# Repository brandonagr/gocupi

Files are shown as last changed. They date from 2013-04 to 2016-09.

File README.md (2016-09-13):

Create Thick TSP
================
forked the code in order to draw thicker lines to get more contrast. For detailed descriptions see file createThickTSP

gocupi
======

Polargraph (vertical plotter / drawing machine) written in Go. Inspired by [Polargraph](http://www.polargraph.co.uk/) and [drawbot](http://marginallyclever.com/blog/drawbot/) projects, designed with the help of the [Dallas Makerspace](http://dallasmakerspace.org/)

Gocupi is different from existing systems in that it uses a Raspberry Pi to do most of the processing instead of relying on a microcontroller to parse commands. This gives it the ability to render complex svg files and patterns that would not fit in memory on a microcontroller.

**A kit with all the hardware needed is now [available at gocupi.com](http://www.gocupi.com/store/)**

Check out the [project page](http://brandonagr.github.io/gocupi/) for a general description, there are also several [wiki pages](https://github.com/brandonagr/gocupi/wiki) with additional information as well as a [forum](http://4um.gocupi.com).

Custom Linux Distro
===================

You can now [download](https://www.dropbox.com/s/6l89m04kcqiwlgb/gocupi_boot_image.zip?dl=0) a custom linux distrobution built from Raspbian with all gocupi software pre-installed.
Unzip the download and copy files to blank SD card (do not build the image). Put the card in the Pi and Bob's your uncle.

If you choose the method above (custom linux distro) then you can skip to the bottom of this document to section "Run gocupi".

Manual Installation Quickstart Guide
================

(Start with something well supported i.e. Raspbian Wheezy.) 

Install Go
-----------
The full install guide is on [golang.org](http://golang.org/doc/install). For the Raspberry Pi you can [download precompiled binaries](http://dave.cheney.net/unofficial-arm-tarballs) to avoid the lengthy process of building go from source.

For example, installing go to the default location with a precompiled binary on a raspberry pi just takes 3 commands:

    wget http://dave.cheney.net/paste/go.1.3.linux-arm~multiarch-armv6-1.tar.gz
    sudo tar -C /usr/local -xzf go.1.3.linux-arm~multiarch-armv6-1.tar.gz
    sudo echo 'export PATH=$PATH:/usr/local/go/bin' >> ~/.profile

(You must set GOROOT also if you install go to someplace besides the default /usr/local/go)

Fix the serial communication (for Raspberry Pi)
----------------------------
Change the default serial communication by editing /boot/cmdline.txt and remove references to `/dev/ttyAMA0`

Disable the getty on that serial port in /etc/inittab by commenting out references to `/dev/ttyAMA0`

In order to reset the serial communication port we need to `sudo reboot`

Setup gopath folder
----------------------------
Setup the folder for your gopath and set some path variables

    mkdir ~/gopath
    sudo echo 'export GOPATH=$HOME/gopath' >> ~/.profile
    sudo echo 'export PATH=$PATH:$HOME/gopath/bin' >> ~/.profile

Install needed dependency
---------------------
Update apt-get, install mercurial, and reboot

    sudo apt-get update
    sudo apt-get install mercurial
    sudo reboot

Download and build gocupi
---------------------------
From your home directory

    go get github.com/brandonagr/gocupi

Run gocupi
----------
`gocupi` The gocupi executable should now be in your $GOPATH\bin folder, you can run the command with no arguments to display the help and what command are available

`gocupi setup 1000 700 700` The setup command can be used to initialize the dimensions of the polargraph hardware, the setup is stored in the generated gocupi_config.xml file

`gocupi -toimage grid 100 10` The -toimage flag causes the system to draw to an output.png instead of trying to control the stepper motors over serial

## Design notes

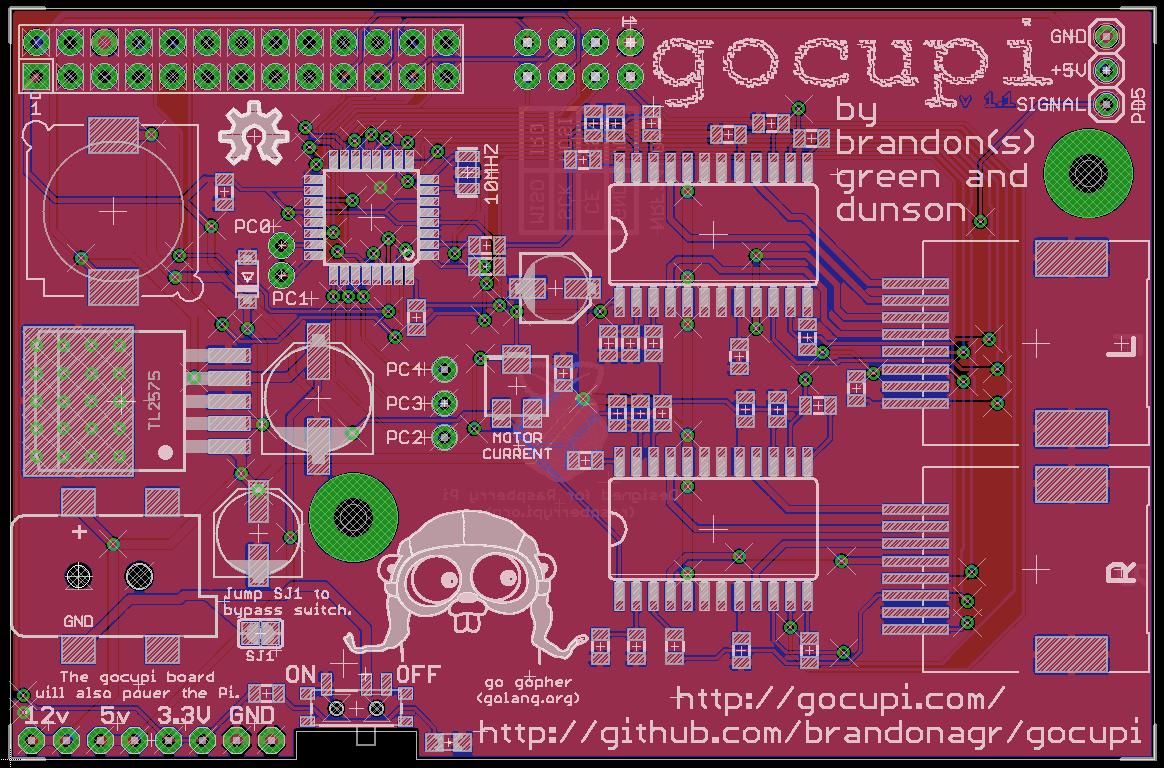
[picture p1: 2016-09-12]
electronics/v1.1/gocupi_v1.1.brd.png

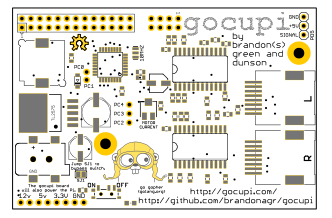
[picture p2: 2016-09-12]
electronics/v1.1/v1.1.png

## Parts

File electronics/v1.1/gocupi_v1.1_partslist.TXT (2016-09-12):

Partlist

Exported from gocupi_v1.1.brd at 9/12/2016 5:10:11 PM

EAGLE Version 6.4.0 Copyright (c) 1988-2013 CadSoft

Assembly variant: 

Part     Value              Package                         Library                     Position (mm)         Orientation

C1       680p               0805                            SparkFun-Passives           (46.51375 8.41375)    R270
C2       100uF              PANASONIC_D                     adafruit                    (18.415 16.8275)      R90
C3       680p               0805                            SparkFun-Passives           (44.45 30.95625)      R270
C4       680p               0805                            SparkFun-Passives           (43.33875 47.3075)    R90
C5       330uF              PANASONIC_F                     adafruit                    (22.86 26.82875)      R90
C7       47uF               PANASONIC_C                     microbuilder                (40.48125 35.08375)   R0
C8       0.1uF              0805                            SparkFun-Passives           (15.875 42.2275)      R270
C9       680p               0805                            SparkFun-Passives           (45.085 25.7175)      R90
CN1                         DCJACK_2MM_SMT                  microbuilder                (5.08 13.6525)        R0
D1                          SOD-123                         dp_devices                  (17.62125 35.71875)   R90
JP1                         1X03-CLEANBIG                   adafruit                    (32.22625 26.51125)   R90
JP2                         1X01-CLEANBIG                   adafruit                    (20.16125 38.25875)   R0
JP3                         1X01-CLEANBIG                   adafruit                    (20.16125 36.03625)   R0
JP4                         1X03                            adafruit                    (81.43875 51.27625)   R90
JP8      Power              1X08-CLEANBIG                   adafruit                    (10.4775 1.42875)     R180
JP9      2X4                2X4                             headers(.1in)               (46.0375 53.34)       R180
L1       220uH              SDR1305                         inductors                   (7.62 40.79875)       R0
LED1                        CHIPLED_0805                    adafruit                    (32.54375 1.27)       R270
R1       10k                0805                            SparkFun-Resistors          (35.40125 36.67125)   R180
R2       1k                 0805                            SparkFun-Resistors          (19.05 4.92125)       R180
R3       20k                0805                            SparkFun-Resistors          (43.815 8.41375)      R90
R4       20k                0805                            SparkFun-Resistors          (46.83125 25.7175)    R270
R5       20k                0805                            SparkFun-Resistors          (46.0375 30.95625)    R90
R6       20k                0805                            SparkFun-Resistors          (44.92625 47.3075)    R270
R7       10k                0805                            SparkFun-Resistors          (35.40125 38.25875)   R180
R8       10k                0805                            SparkFun-Resistors          (30.1625 32.86125)    R90
R9       10k                0805                            SparkFun-Resistors          (62.865 27.6225)      R270
R11      10k                0805                            SparkFun-Resistors          (59.21375 31.4325)    R90
R12      10k                SM-42/43A                       pot                         (37.62375 27.78125)   R270
R13      10k                0805                            SparkFun-Resistors          (47.78375 30.95625)   R90
R14      10k                0805                            SparkFun-Resistors          (49.37125 8.41375)    R90
R15      10k                0805                            SparkFun-Resistors          (60.0075 26.3525)     R0
R16      10k                0805                            SparkFun-Resistors          (59.3725 8.09625)     R90
R17      10k                0805                            SparkFun-Resistors          (56.99125 26.035)     R270
R18      10k                0805                            SparkFun-Resistors          (56.515 47.3075)      R0
R19      10k                0805                            SparkFun-Resistors          (47.625 47.3075)      R270
R20      5k1                0805                            SparkFun-Resistors          (41.11625 28.73375)   R270
R21      0.75               0805                            SparkFun-Resistors          (54.61 26.035)        R270
R22      0.75               0805                            SparkFun-Resistors          (54.2925 8.09625)     R90
R23      0.75               0805                            SparkFun-Resistors          (54.13375 30.00375)   R90
R24      0.75               0805                            SparkFun-Resistors          (53.34 46.51375)      R0
R25      10k                0805                            SparkFun-Passives           (59.53125 46.19625)   R0
R26      10k                0805                            SparkFun-Resistors          (42.545 44.60875)     R0
R27      10k                0805                            SparkFun-Resistors          (48.41875 25.7175)    R270
R28      10k                0805                            SparkFun-Resistors          (42.70375 22.225)     R0
RJ45-L   RJ45_SMD           RJ45_SMD                        rj45_smd                    (76.2 30.95625)       R90
RJ45-R   RJ45_SMD           RJ45_SMD                        rj45_smd                    (76.2 14.12875)       R90
S1                          SWITCH-SPST-SMD-A               SwK-SparkFun                (25.7175 3.81)        R180
SJ1      SJ1                SJ                              jumper                      (18.57375 9.36625)    R180
U1                          TQFP32-08                       SparkFun-DigitalIC          (26.82875 40.3225)    R180
U2       A3967SLB-L         SO24W                           allegro                     (52.22875 39.0525)    R0
U3       A3967SLB-R         SO24W                           allegro                     (52.22875 17.145)     R0
U4       TL2575             TO263_5                         TL2575_new                  (8.255 26.67)         R90
X1       RASPI_BOARD_AB_E2P RASPI_BOARD_AB_EDGES_2DRILL_PAD raspberrypi_bastelstube_v13 (0 0)                 R0
XTAL1    10MHz              RESONATOR-SMD                   SwK-SparkFun                (33.9725 43.65625)    R90

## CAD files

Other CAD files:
cad/motor mount.dwg
cad/small bearing holder.dwg
cad/guide.dwg

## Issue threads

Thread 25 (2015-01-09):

minor request:  When canceling, print the pen location relative to the starting position

andrewshilliday, 2015-01-09:
It would be nice if, when canceling a print, the program would print out the current location of the pen (in mm for each motor to spool) to get the pen back to the original location so that you don't have to recalibrate to start over.

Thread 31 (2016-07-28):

Trying to DIY this. Any thoughts?

campbx, 2016-07-28:
Hey Brandon, sorry couldn't find your DM/Email, so communicating through an issue.

I am trying to DIY this Zen sand garden using your project:
https://vimeo.com/124882379
You can see more videos inside the artist's gallery.

What would it entail to covert Gocupi kit in a horizontal setup?  I will use a Gocupi-controlled Neodymium magnet underneath a glass surface, and sand + metal ball on the top of the surface.

brandonagr, 2016-08-08:
It would take a lot of work to rewrite a large portion of the code to use a more traditional XY based coordinate system instead of the 'polar' system of two string lengths used here. src/plotter/driver.go is the code that converts the XY coordinates to 'polar', everything downstream of that would have to change

scottvr, 2016-08-08:
What brandonagr is certainly correct, however I did successfully use the gocupi horizontally as is. Your surface would need to be sufficiently elevated to pull it off the same way I did my silly hack, but I'll describe it here for posterity.

[post-edit. Whoa! That got long. Apologies. **TL;DR.: If your surface is elevated, you can attach a counterweight to the gondola and have a horizontally-mounted vertical plotter.** :-) You could then attach a strong magnet to the gondola and a glass table sitting over it - in fact, you might just stick some minature casters or bearings on the bottom of something more suited for the purpose than a pen-holder gondola and you can forego the added consideration of keeping the gondola elevated from the surface below it, since you won't then have weight bearing down on a small pen-tip and woblling and such. But I've rambled long enough so I really will stop now.]

The hanging vertical plotter mechanism relies on the magical invisible pulling force of gravity (and thus the weight of the gondola) to keep the string lengths taught and straight. The top of the drawing surface (imagine a line between the two motors) and the two string lengths form a triangle, with the motors and gondola at each vertex.

Briefly, I had the thought that two more motors opposite the original two would be needed for horizontal success, which while not being complex mathematically or programatically to add them, how to set the initial position, keeping all four lines taught and not having the motors battling against each other was to much to entertain for a silly proof of concept.

But then I thought of that invisible "motor" (gravity) pulling downward on the gondola now, and realized only one additional motor would be needed, perhaps on a rod parallell to the invisible line between the "top" motors.. Visions of a truly ludicrous setup with a bottom "slack" stepper perpendicular to the invisible line, with its own X-axis motion briefly made me chuckle before I realized that a rubber band on a spool over a dowel would meet both purposes, although the further the gondola moved away from this rod, the greater the force pulling the gondola toward it and then things I can barely remember about elastic potential energy and unpleasant memories of the physics class I failed where I should have learned it shut down the thought experiment for the moment. But then, with the vision of the horizontal surface, motors on one side, and a rod running the length of the other still rattling around in the back of my head, it occurred to me that I could attach a string with the surprising properties of (nearly) always (nearly) exerting the same amount of horizontal force away fro the steppers which (not) coincidentally happens to be (nearly) exactly 9.8ms^s. Those of you who passed the physics I failed no doubt immediately recognize that as the acceleration of gravity and probably see where I'm going with this.

So... I laid a whiteboard horizontally on the trunk of my '61 Biscayne, which conveniently already had gocupi motor mounts suction-cupped in place (the board, not my car.. but there's a different story for a different time) and a gondola hanging in the center. I affixed a length of string the length of the "height" (these terms are getting confusing as we move our Euclidian plan in 3D space,  for me at least) of the whitboard + the elevation of the now-horizontal whiteboard from the ground. With the edge of the "bottom" (the 2D bottom, from back when it was in a vertical plane... this is why instructional diagrams label things with convenient unambiguous letters, isn't it?) anyway.. with the side of the whiteboard that used to be the bottom now hanging just beyond the edge of the trunk of the Chevy, and using washers, cable and wire guides and fasteners and other various sundries found in my garage, dangled this weighted line from the gondola over the edge of the whiteboard so that the washers now moved vertically up and down with the movement of the gondola on the whiteboard's Y-axis. With just enough weight from the washers to counteract the gravity that is now tending to draw the gondola to the board, and just enough height from the rod/wire guides/whathaveyou, I was able to replicate the vertical conditions faithfully enough to fool the gocupi into drawing for me as if it was still vertical.

If my writing was too confusing - perhaps a visual illustration would help. But I'm not going to take up any more space with ASCII art so I will leave you with this.. Do you remember the old Batman TV series from the 1960's? Do you remember the scenes where Batman and Robin would be scaling the side of a skyscraper by holding a rope hanging from the top of the building? And how even as a kid watching this, the occasional slack in the rope or other visual cues enabled even a 5-year-old to give the TV a side-eyed glare.. and then, with their innocent little imagination-filled heads turned sideways, they have a Eureka! moment when they realize "hey.... they're just walking and the camera is turned sideways!", and that innocence that enables the perfect suspension of disbelief is forever lost? Yeah, will I'm not saying it's like that, but it's like that.

Closed 2016-08-08.

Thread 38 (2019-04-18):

Left and right stop switches.

monte-monte, 2019-04-18:
Hello. I'm building myself a plotter using your code and schematics. On schematics steppers have stop switches which are connected to atmega pins. But strangely I haven't found any code related to them in "StepperDriver.ino". I would like to know which part is outdated here, or those switches are just for future features like auto-calibration that haven't been implemented yet?

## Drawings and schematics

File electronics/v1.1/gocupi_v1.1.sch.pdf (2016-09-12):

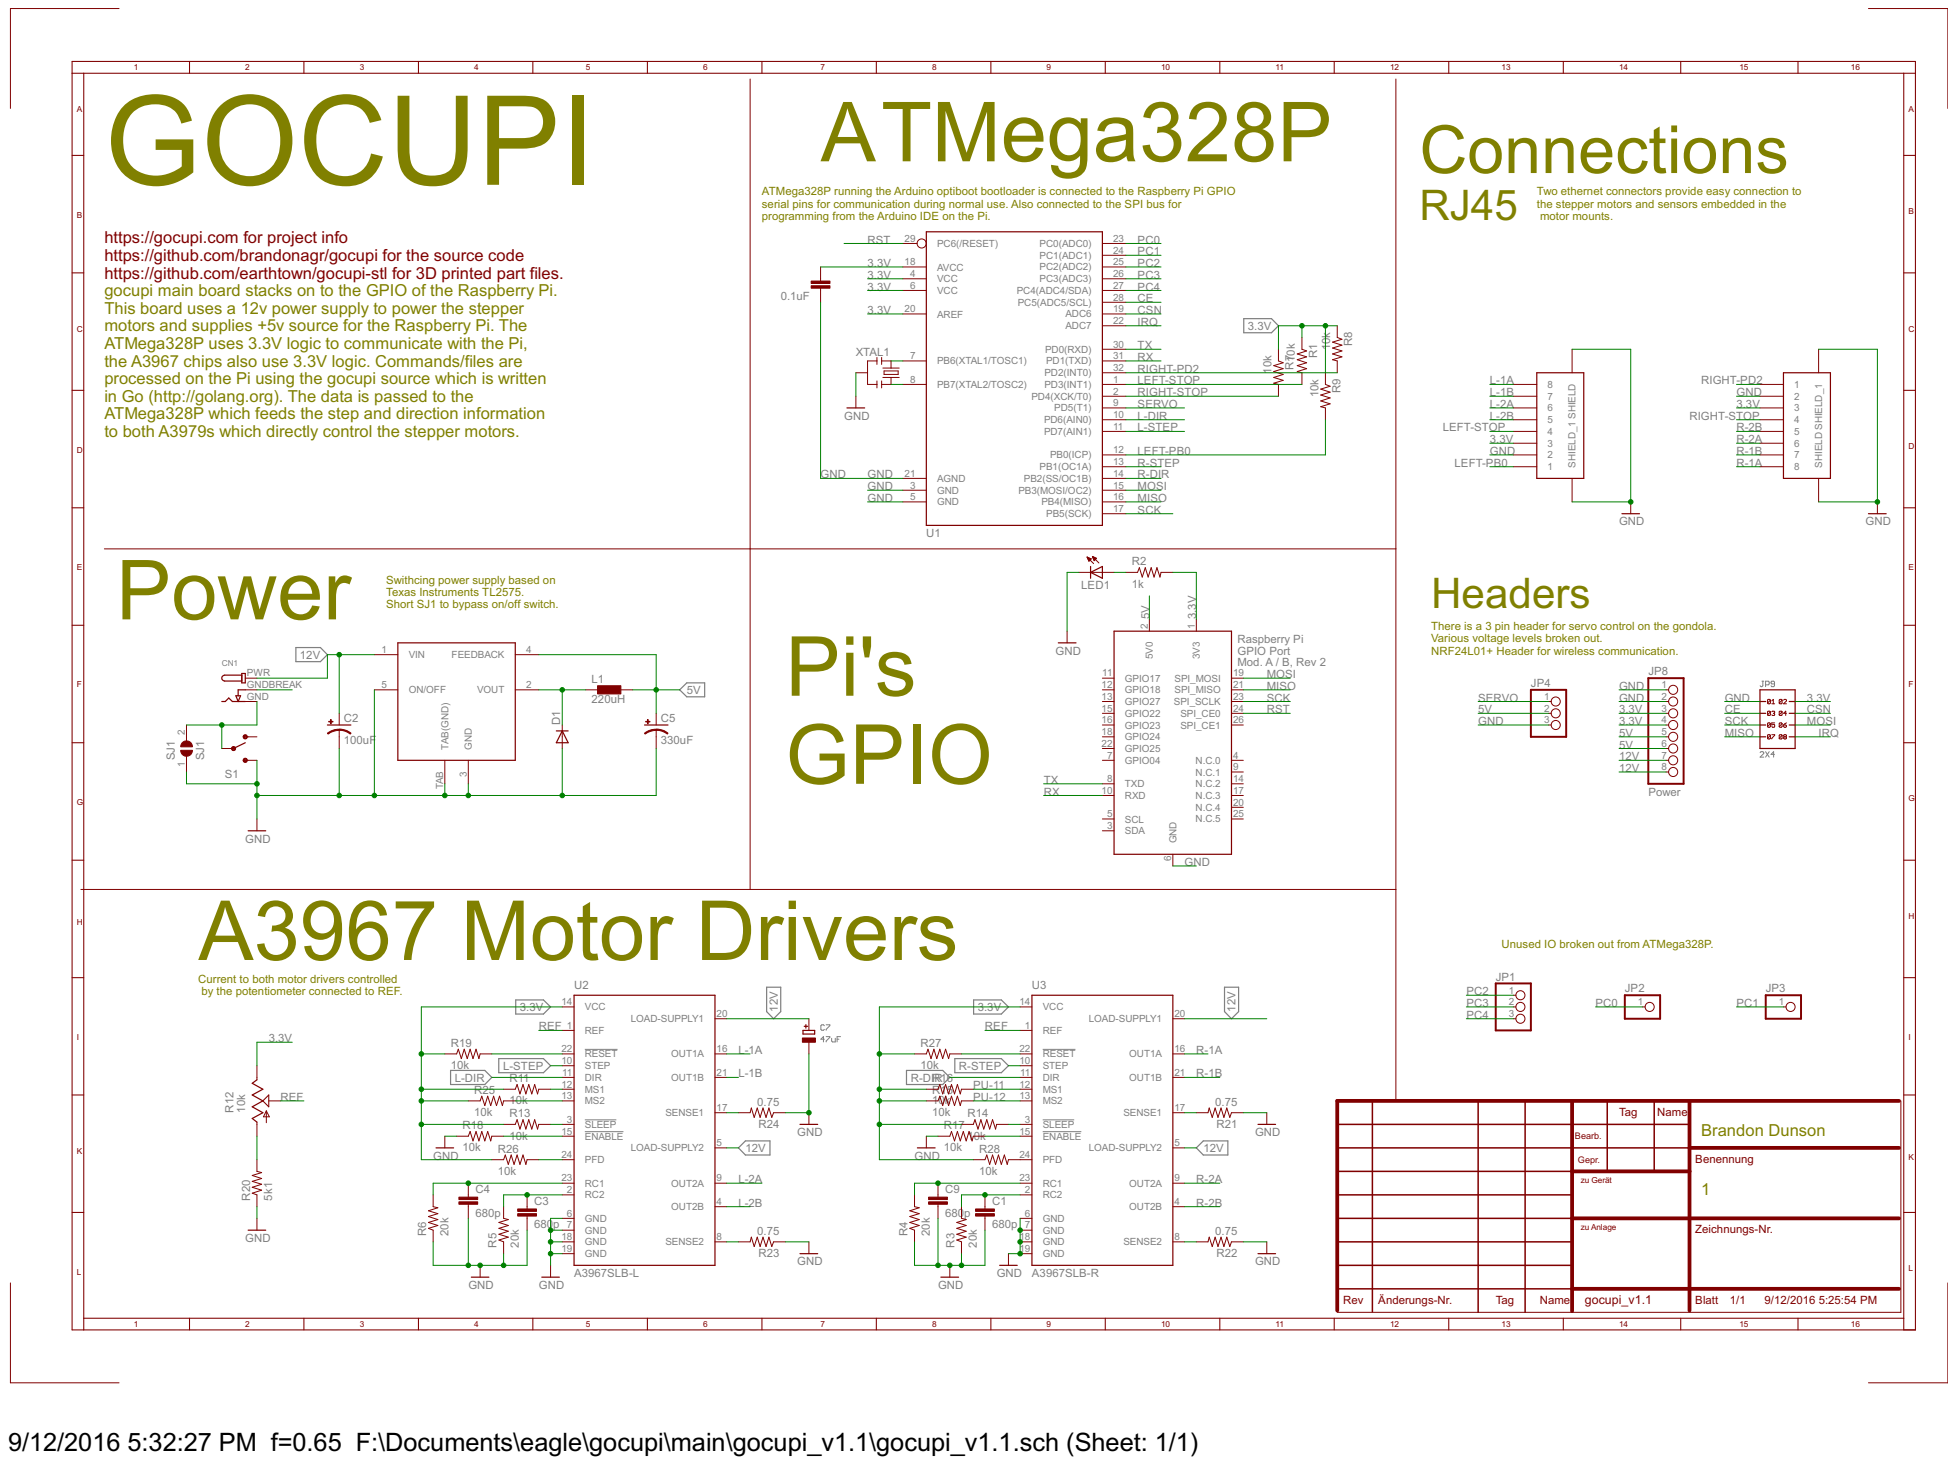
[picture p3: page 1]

ATMega328P ATMega328P running the Arduino optiboot bootloader is connected to the Raspberry Pi GPIO | Connections Two ethernet connectors provide easy connection to the stepper motors and sensors embedded in the motor mounts. | A

https://gocupi.com for project info
https://github.com/brandonagr/gocupi for the source code
https://github.com/earthtown/gocupi-stl for 3D printed part files.
gocupi main board stacks on to the GPIO of the Raspberry Pi. This board uses a 12v power supply to power the stepper motors and supplies +5v source for the Raspberry Pi. The ATMega328P uses 3.3V logic to communicate with the Pi,

the A3967 chips also use 3.3V logic. Commands/files are
processed on the Pi using the gocupi source which is written
in Go (http://golang.org). The data is passed to the ATMega328P which feeds the step and direction information

to both A3979s which directly control the stepper motors.
Power

Short SJ1 to bypass on/off switch. Swithcing power supply based on Texas Instruments TL2575.

Raspberry Pi GPIO Port Mod. A / B, Rev 2 GND

There is a 3 pin header for servo control on the gondola. Various voltage levels broken out. NRF24L01+ Header for wireless communication.

Unused IO broken out from ATMega328P.

Current to both motor drivers controlled
by the potentiometer connected to REF.

9/12/2016 5:32:27 PM f=0.65 F:\Documents\eagle\gocupi\main\gocupi_v1.1\gocupi_v1.1.sch (Sheet: 1/1)

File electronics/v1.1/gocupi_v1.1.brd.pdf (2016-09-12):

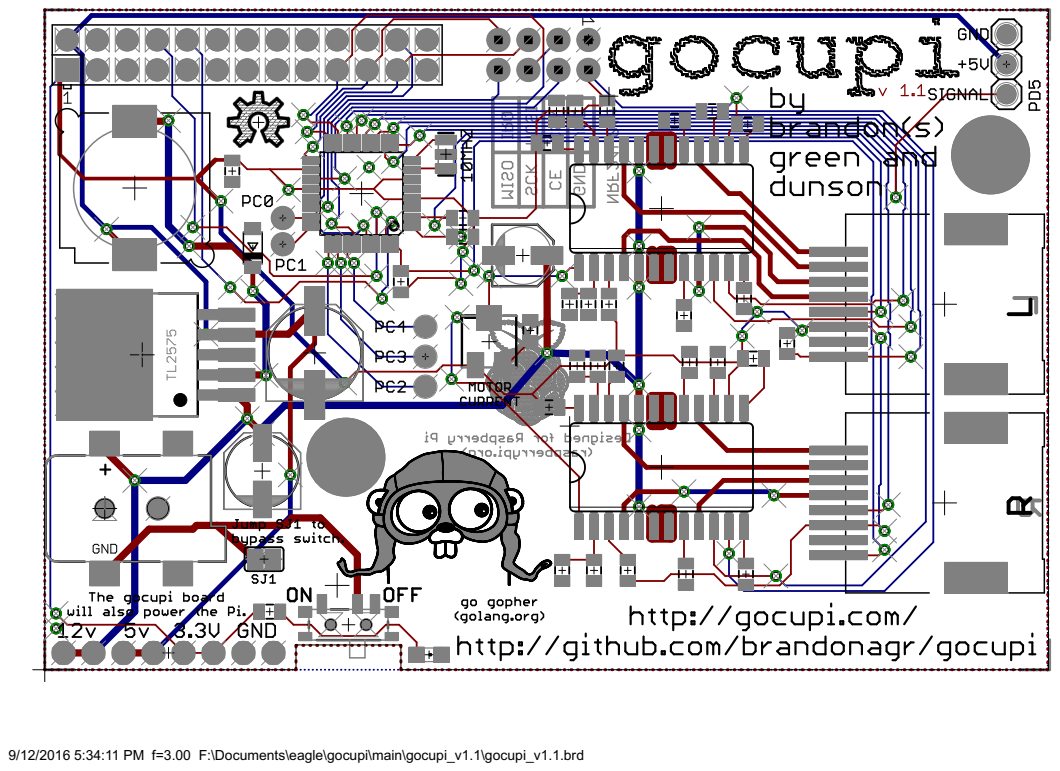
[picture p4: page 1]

9/12/2016 5:34:11 PM f=3.00 F:\Documents\eagle\gocupi\main\gocupi_v1.1\gocupi_v1.1.brd

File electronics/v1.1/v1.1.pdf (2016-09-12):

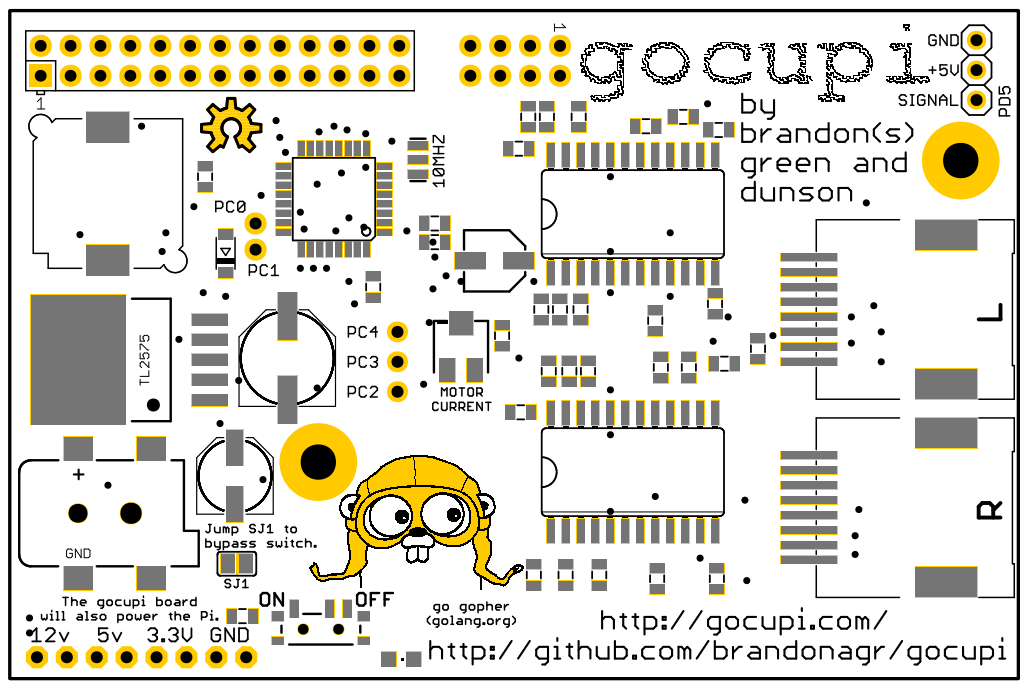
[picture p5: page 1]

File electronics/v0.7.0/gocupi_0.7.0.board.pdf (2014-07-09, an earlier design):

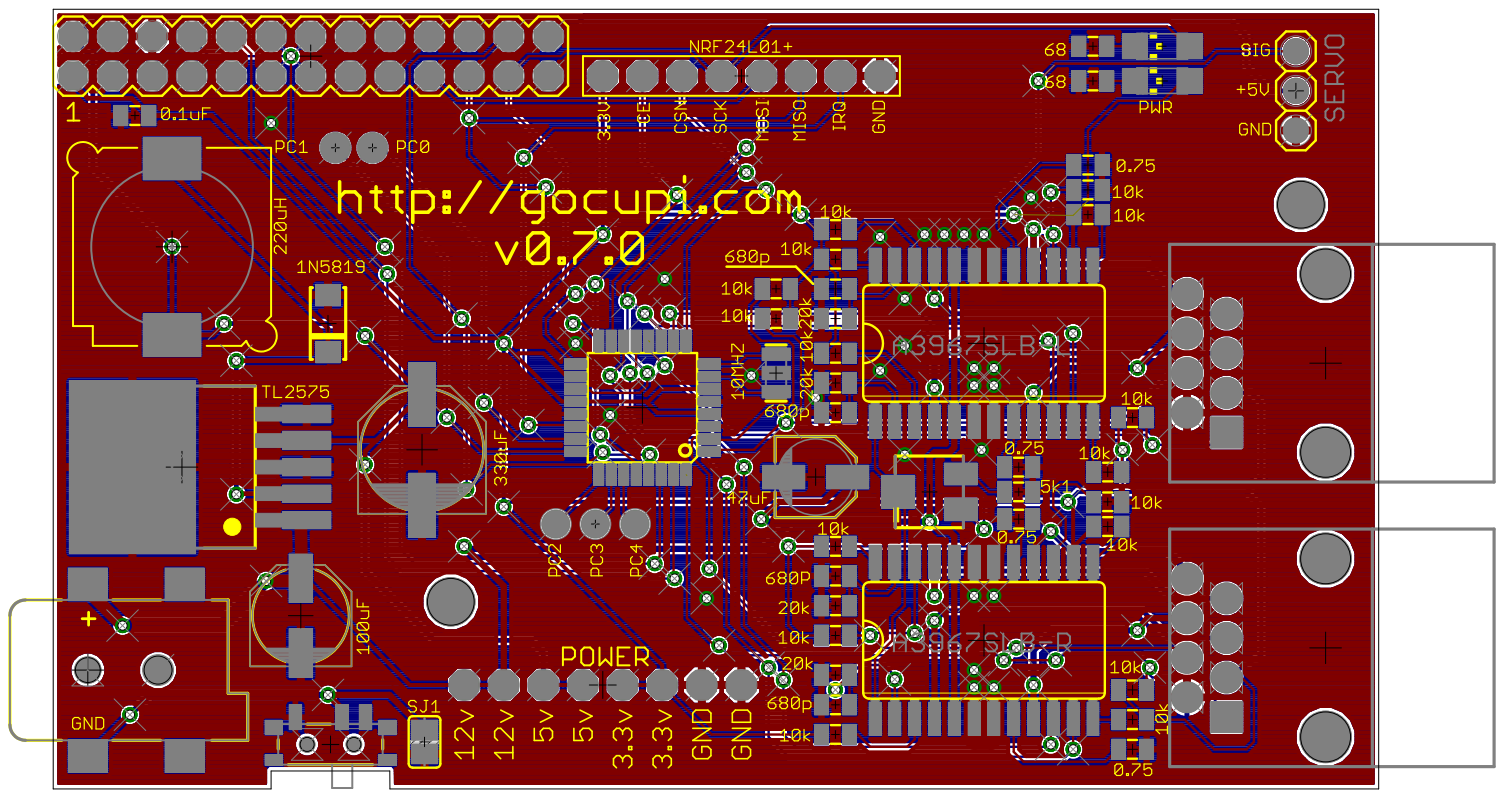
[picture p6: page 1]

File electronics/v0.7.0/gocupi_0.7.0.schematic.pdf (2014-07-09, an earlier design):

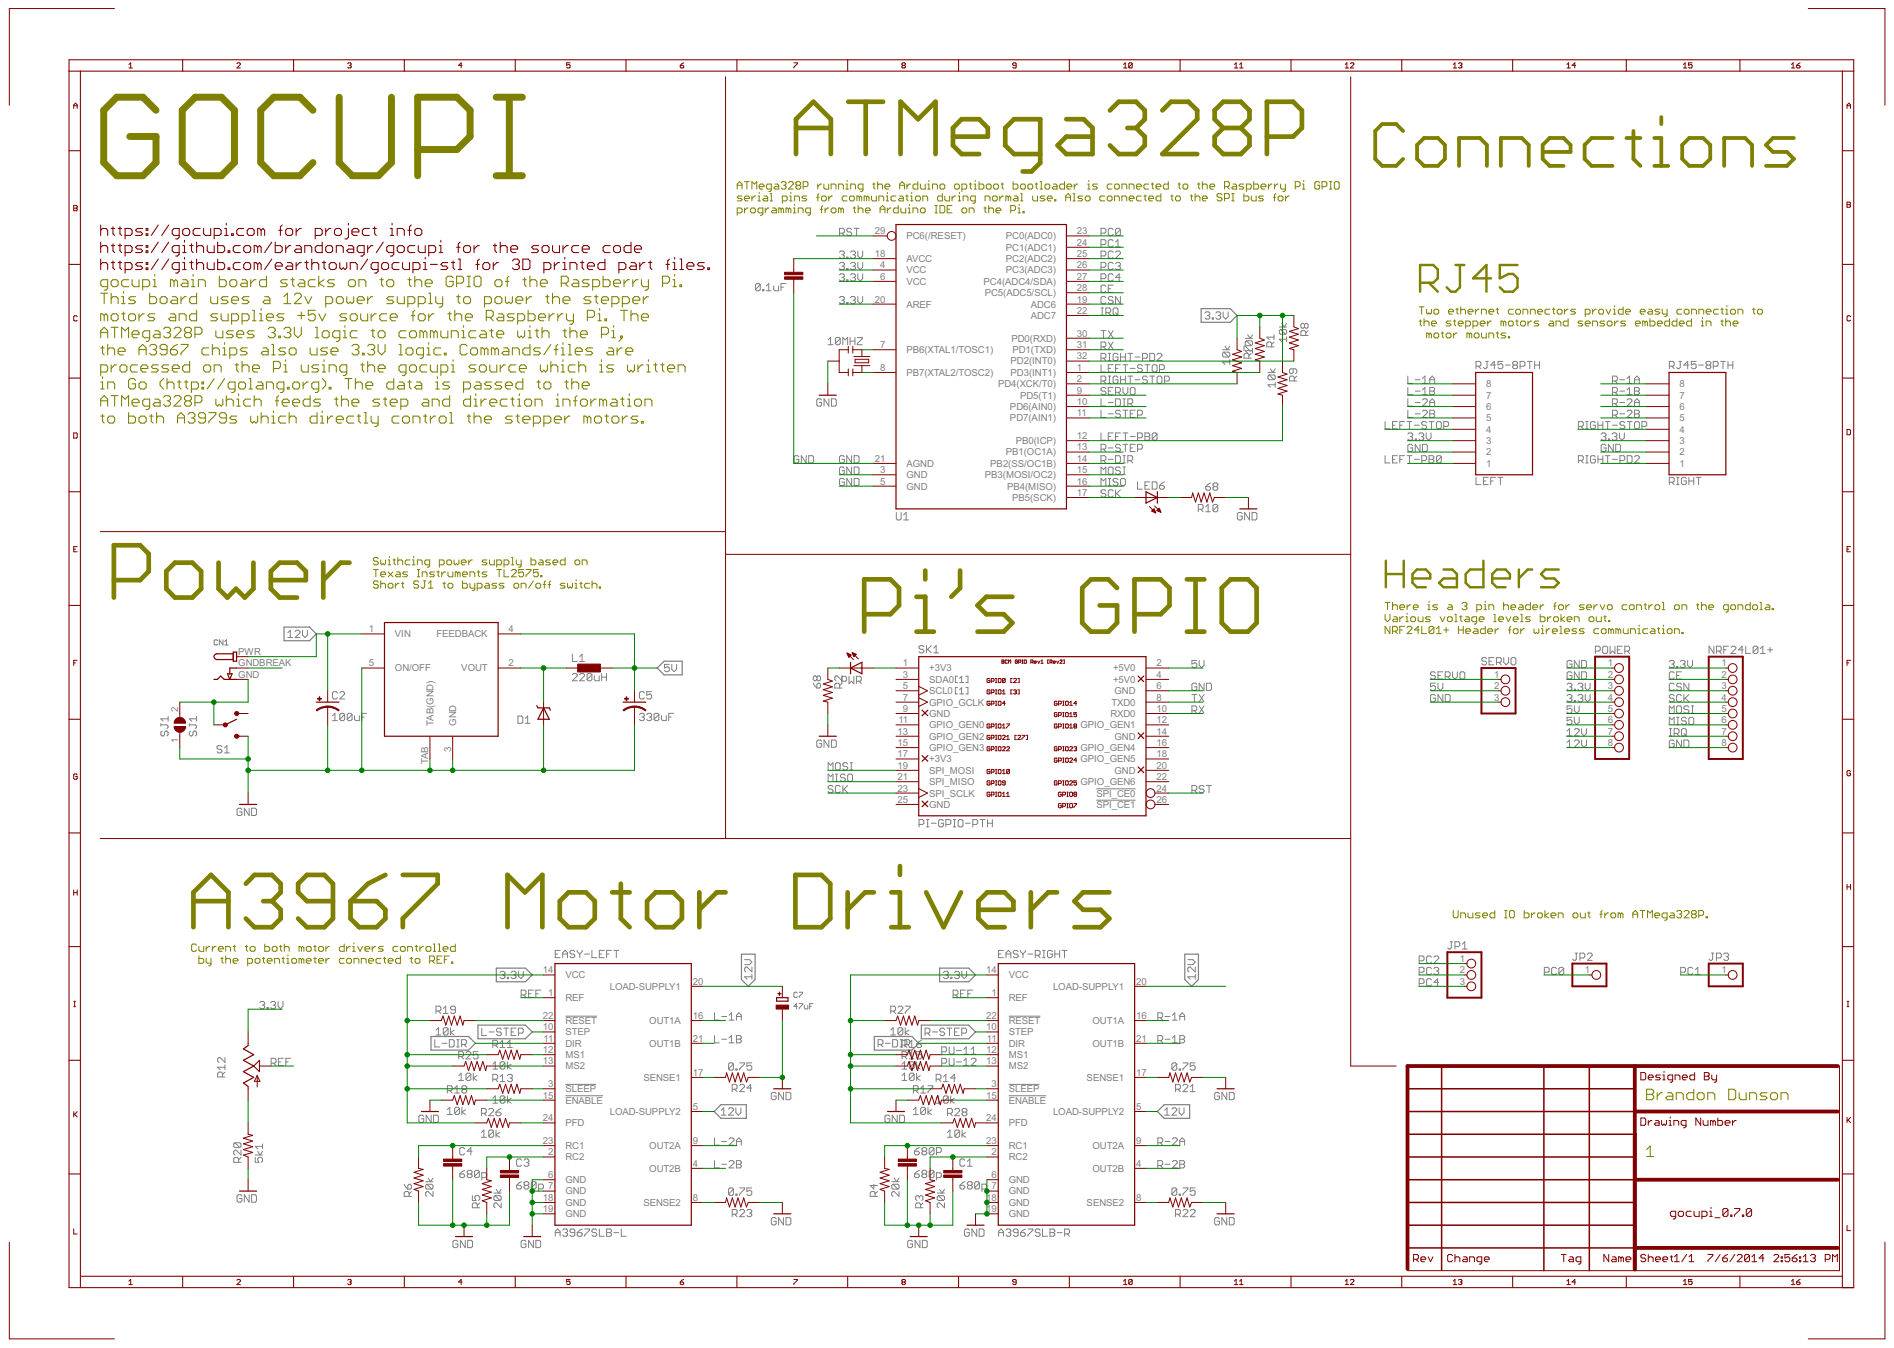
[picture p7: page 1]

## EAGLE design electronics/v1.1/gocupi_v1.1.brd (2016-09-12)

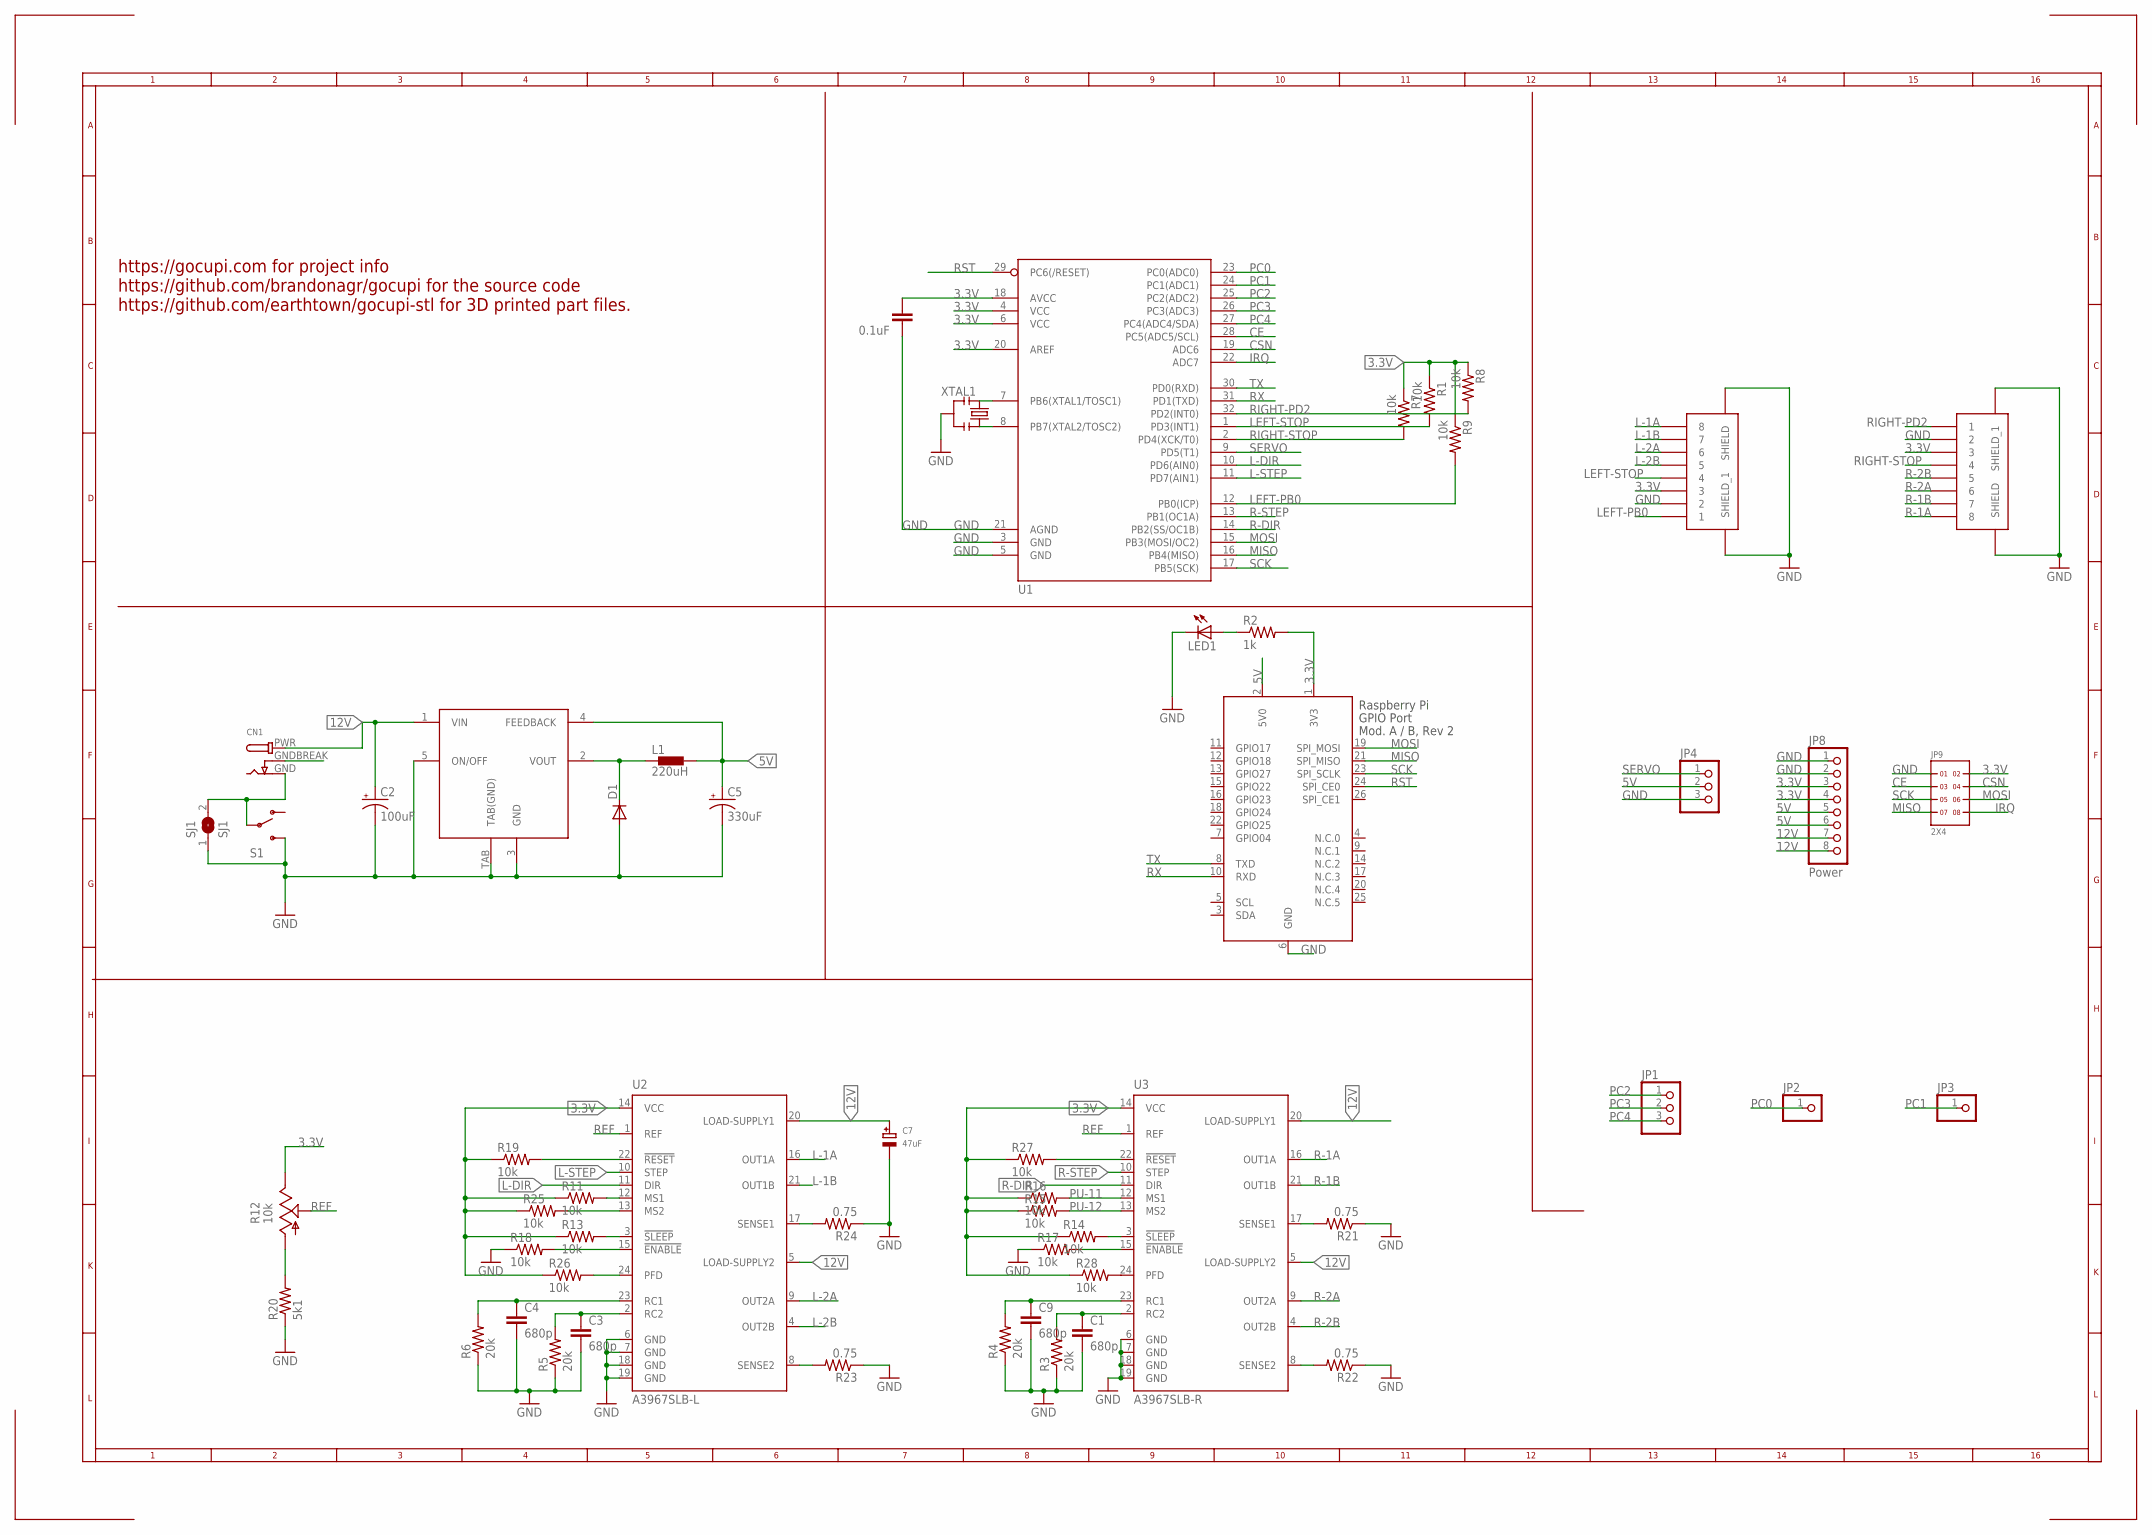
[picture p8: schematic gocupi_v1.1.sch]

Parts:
C1, C3, C4, C9: 680p; 0805
C2: 100uF; PANASONIC_D
C5: 330uF; PANASONIC_F
C7: 47uF; PANASONIC_C
C8: 0.1uF; 0805
CN1: DCBARRELSMT_CORRECT; DCJACK_2MM_SMT
D1: DIODE-SOD-123; SOD-123
JP1: PINHD-1X3CB; 1X03-CLEANBIG
JP2, JP3: PINHD-1X1CB; 1X01-CLEANBIG
JP4: PINHD-1X3; 1X03
JP8: Power; 1X08-CLEANBIG
JP9: 2X4
L1: 220uH; SDR1305
LED1: LEDCHIPLED_0805; CHIPLED_0805
R1, R7, R8, R9, R11, R13, R14, R15, R16, R17, R18, R19, R25, R26, R27, R28: 10k; 0805
R2: 1k; 0805
R3, R4, R5, R6: 20k; 0805
R12: 10k; SM-42/43A
R20: 5k1; 0805
R21, R22, R23, R24: 0.75; 0805
RJ45-L, RJ45-R: RJ45_SMD
S1: SWITCH-SPST-SMD-A
SJ1: SJ1; SJ
U1: ATMEGA328_SMT; TQFP32-08
U2: A3967SLB-L; SO24W
U3: A3967SLB-R; SO24W
U4: TL2575; TO263_5
X1: RASPI_BOARD_AB_E2P; RASPI_BOARD_AB_EDGES_2DRILL_PAD
XTAL1: 10MHz; RESONATOR-SMD

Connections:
3.3V: C8.1, JP8.3, JP8.4, JP9.2, R1.1, R2.2, R7.1, R8.1, R9.1, R11.1, R12.3 (E), R13.1, R14.1, R15.1, R16.1, R19.1, R25.1, R26.1, R27.1, R28.1, RJ45-L.P$3 (3), RJ45-R.P$3 (3), U1.4 (VCC), U1.6 (VCC), U1.18 (AVCC), U1.20 (AREF), U2.14 (VCC), U3.14 (VCC), X1.1 (3V3)
5V: C5.+, JP4.2, JP8.5, JP8.6, L1.P$2 (2), U4.4 (FEEDBACK), X1.2 (5V0)
12V: C2.+, C7.+, CN1.PWR, JP8.7, JP8.8, U2.5 (LOAD-SUPPLY2), U2.20 (LOAD-SUPPLY1), U3.5 (LOAD-SUPPLY2), U3.20 (LOAD-SUPPLY1), U4.1 (VIN)
B-GND: CN1.GNDBREAK
CE: JP9.3, U1.28 (PC5(ADC5/SCL))
CSN: JP9.4, U1.19 (ADC6)
GND: C1.2, C2.-, C3.2, C4.2, C5.-, C7.-, C8.2, C9.2, D1.A, JP4.3, JP8.1, JP8.2, JP9.1, LED1.C, R3.1, R4.1, R5.1, R6.1, R17.1, R18.1, R20.1, R21.1, R22.1, R23.1, R24.1, RJ45-L.P$2 (2), RJ45-L.P$SHIELD (SHIELD), RJ45-L.P$SHIELD_1 (SHIELD_1), RJ45-R.P$2 (2), RJ45-R.P$SHIELD (SHIELD), RJ45-R.P$SHIELD_1 (SHIELD_1), S1.3 (S), SJ1.1, U1.3 (GND), U1.5 (GND), U1.21 (AGND), U2.6 (GND), U2.7 (GND), U2.18 (GND), U2.19 (GND), U3.6 (GND), U3.7 (GND), U3.18 (GND), U3.19 (GND), U4.3 (GND), U4.5 (ON/OFF), U4.TAB (TAB(GND)), X1.6 (GND), XTAL1.2
IRQ: JP9.8, U1.22 (ADC7)
L-1A: RJ45-L.P$8 (8), U2.16 (OUT1A)
L-1B: RJ45-L.P$7 (7), U2.21 (OUT1B)
L-2A: RJ45-L.P$6 (6), U2.9 (OUT2A)
L-2B: RJ45-L.P$5 (5), U2.4 (OUT2B)
L-DIR: U1.10 (PD6(AIN0)), U2.11 (DIR)
L-STEP: U1.11 (PD7(AIN1)), U2.10 (STEP)
LEFT-PB0: R9.2, RJ45-L.P$1 (1), U1.12 (PB0(ICP))
LEFT-STOP: R1.2, RJ45-L.P$4 (4), U1.1 (PD3(INT1))
MISO: JP9.7, U1.16 (PB4(MISO)), X1.21 (SPI_MISO)
MOSI: JP9.6, U1.15 (PB3(MOSI/OC2)), X1.19 (SPI_MOSI)
unnamed: D1.C, L1.P$1 (1), U4.2 (VOUT)
unnamed: CN1.GND, S1.2, SJ1.2
unnamed: LED1.A, R2.1
unnamed: R28.2, U3.24 (PFD)
unnamed: R19.2, U2.22 (!RESET)
unnamed: R11.2, U2.12 (MS1)
unnamed: R26.2, U2.24 (PFD)
unnamed: R27.2, U3.22 (!RESET)
unnamed: R25.2, U2.13 (MS2)
unnamed: R17.2, U3.15 (!ENABLE)
unnamed: R14.2, U3.3 (!SLEEP)
unnamed: R13.2, U2.3 (!SLEEP)
unnamed: R12.1 (A), R20.2
unnamed: R18.2, U2.15 (!ENABLE)
unnamed: C4.1, R6.2, U2.23 (RC1)
unnamed: C3.1, R5.2, U2.2 (RC2)
unnamed: R24.2, U2.17 (SENSE1)
unnamed: R21.2, U3.17 (SENSE1)
unnamed: R23.2, U2.8 (SENSE2)
unnamed: C9.1, R4.2, U3.23 (RC1)
unnamed: R22.2, U3.8 (SENSE2)
unnamed: C1.1, R3.2, U3.2 (RC2)
unnamed: U1.7 (PB6(XTAL1/TOSC1)), XTAL1.1
unnamed: U1.8 (PB7(XTAL2/TOSC2)), XTAL1.3
PC0: JP2.1, U1.23 (PC0(ADC0))
PC1: JP3.1, U1.24 (PC1(ADC1))
PC2: JP1.1, U1.25 (PC2(ADC2))
PC3: JP1.2, U1.26 (PC3(ADC3))
PC4: JP1.3, U1.27 (PC4(ADC4/SDA))
PU-11: R16.2, U3.12 (MS1)
PU-12: R15.2, U3.13 (MS2)
R-1A: RJ45-R.P$8 (8), U3.16 (OUT1A)
R-1B: RJ45-R.P$7 (7), U3.21 (OUT1B)
R-2A: RJ45-R.P$6 (6), U3.9 (OUT2A)
R-2B: RJ45-R.P$5 (5), U3.4 (OUT2B)
R-DIR: U1.14 (PB2(SS/OC1B)), U3.11 (DIR)
R-STEP: U1.13 (PB1(OC1A)), U3.10 (STEP)
REF: R12.2 (S), U2.1 (REF), U3.1 (REF)
RIGHT-PD2: R8.2, RJ45-R.P$1 (1), U1.32 (PD2(INT0))
RIGHT-STOP: R7.2, RJ45-R.P$4 (4), U1.2 (PD4(XCK/T0))
RST: U1.29 (PC6(/RESET)), X1.24 (SPI_CE0)
RX: U1.31 (PD1(TXD)), X1.10 (RXD)
SCK: JP9.5, U1.17 (PB5(SCK)), X1.23 (SPI_SCLK)
SERVO: JP4.1, U1.9 (PD5(T1))
TX: U1.30 (PD0(RXD)), X1.8 (TXD)

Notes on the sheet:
https://gocupi.com for project info https://github.com/brandonagr/gocupi for the source code https://github.com/earthtown/gocupi-stl for 3D printed part files.

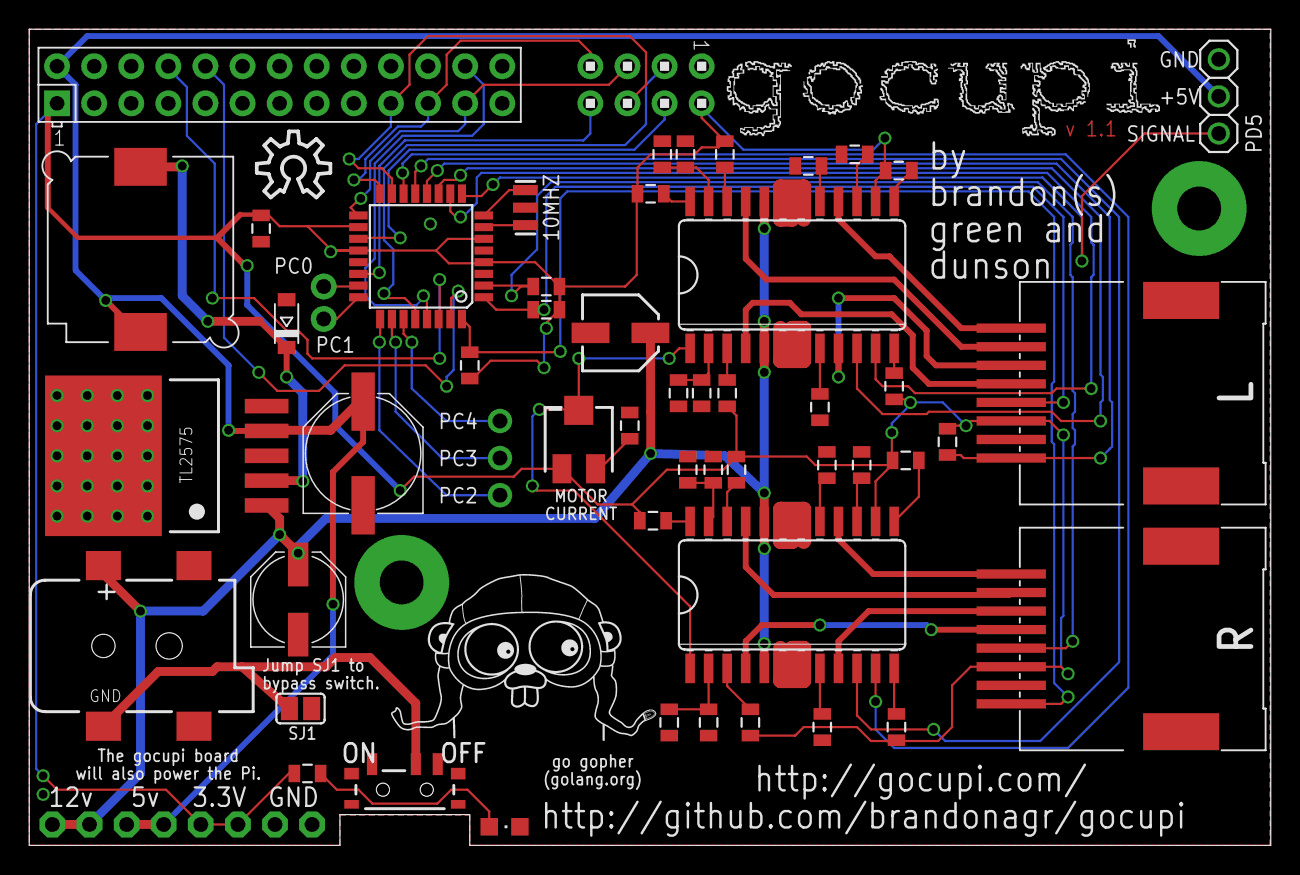
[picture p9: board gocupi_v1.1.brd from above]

Board: 4 copper layers, 85.0 x 55.9 mm, 59 parts (1 on the bottom side), 62 nets.

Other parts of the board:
U$1: OSHWLOGO_TOP_0.2
U$2: LETTERS
U$3: GO_BLACK
U$5: PI_BLACK

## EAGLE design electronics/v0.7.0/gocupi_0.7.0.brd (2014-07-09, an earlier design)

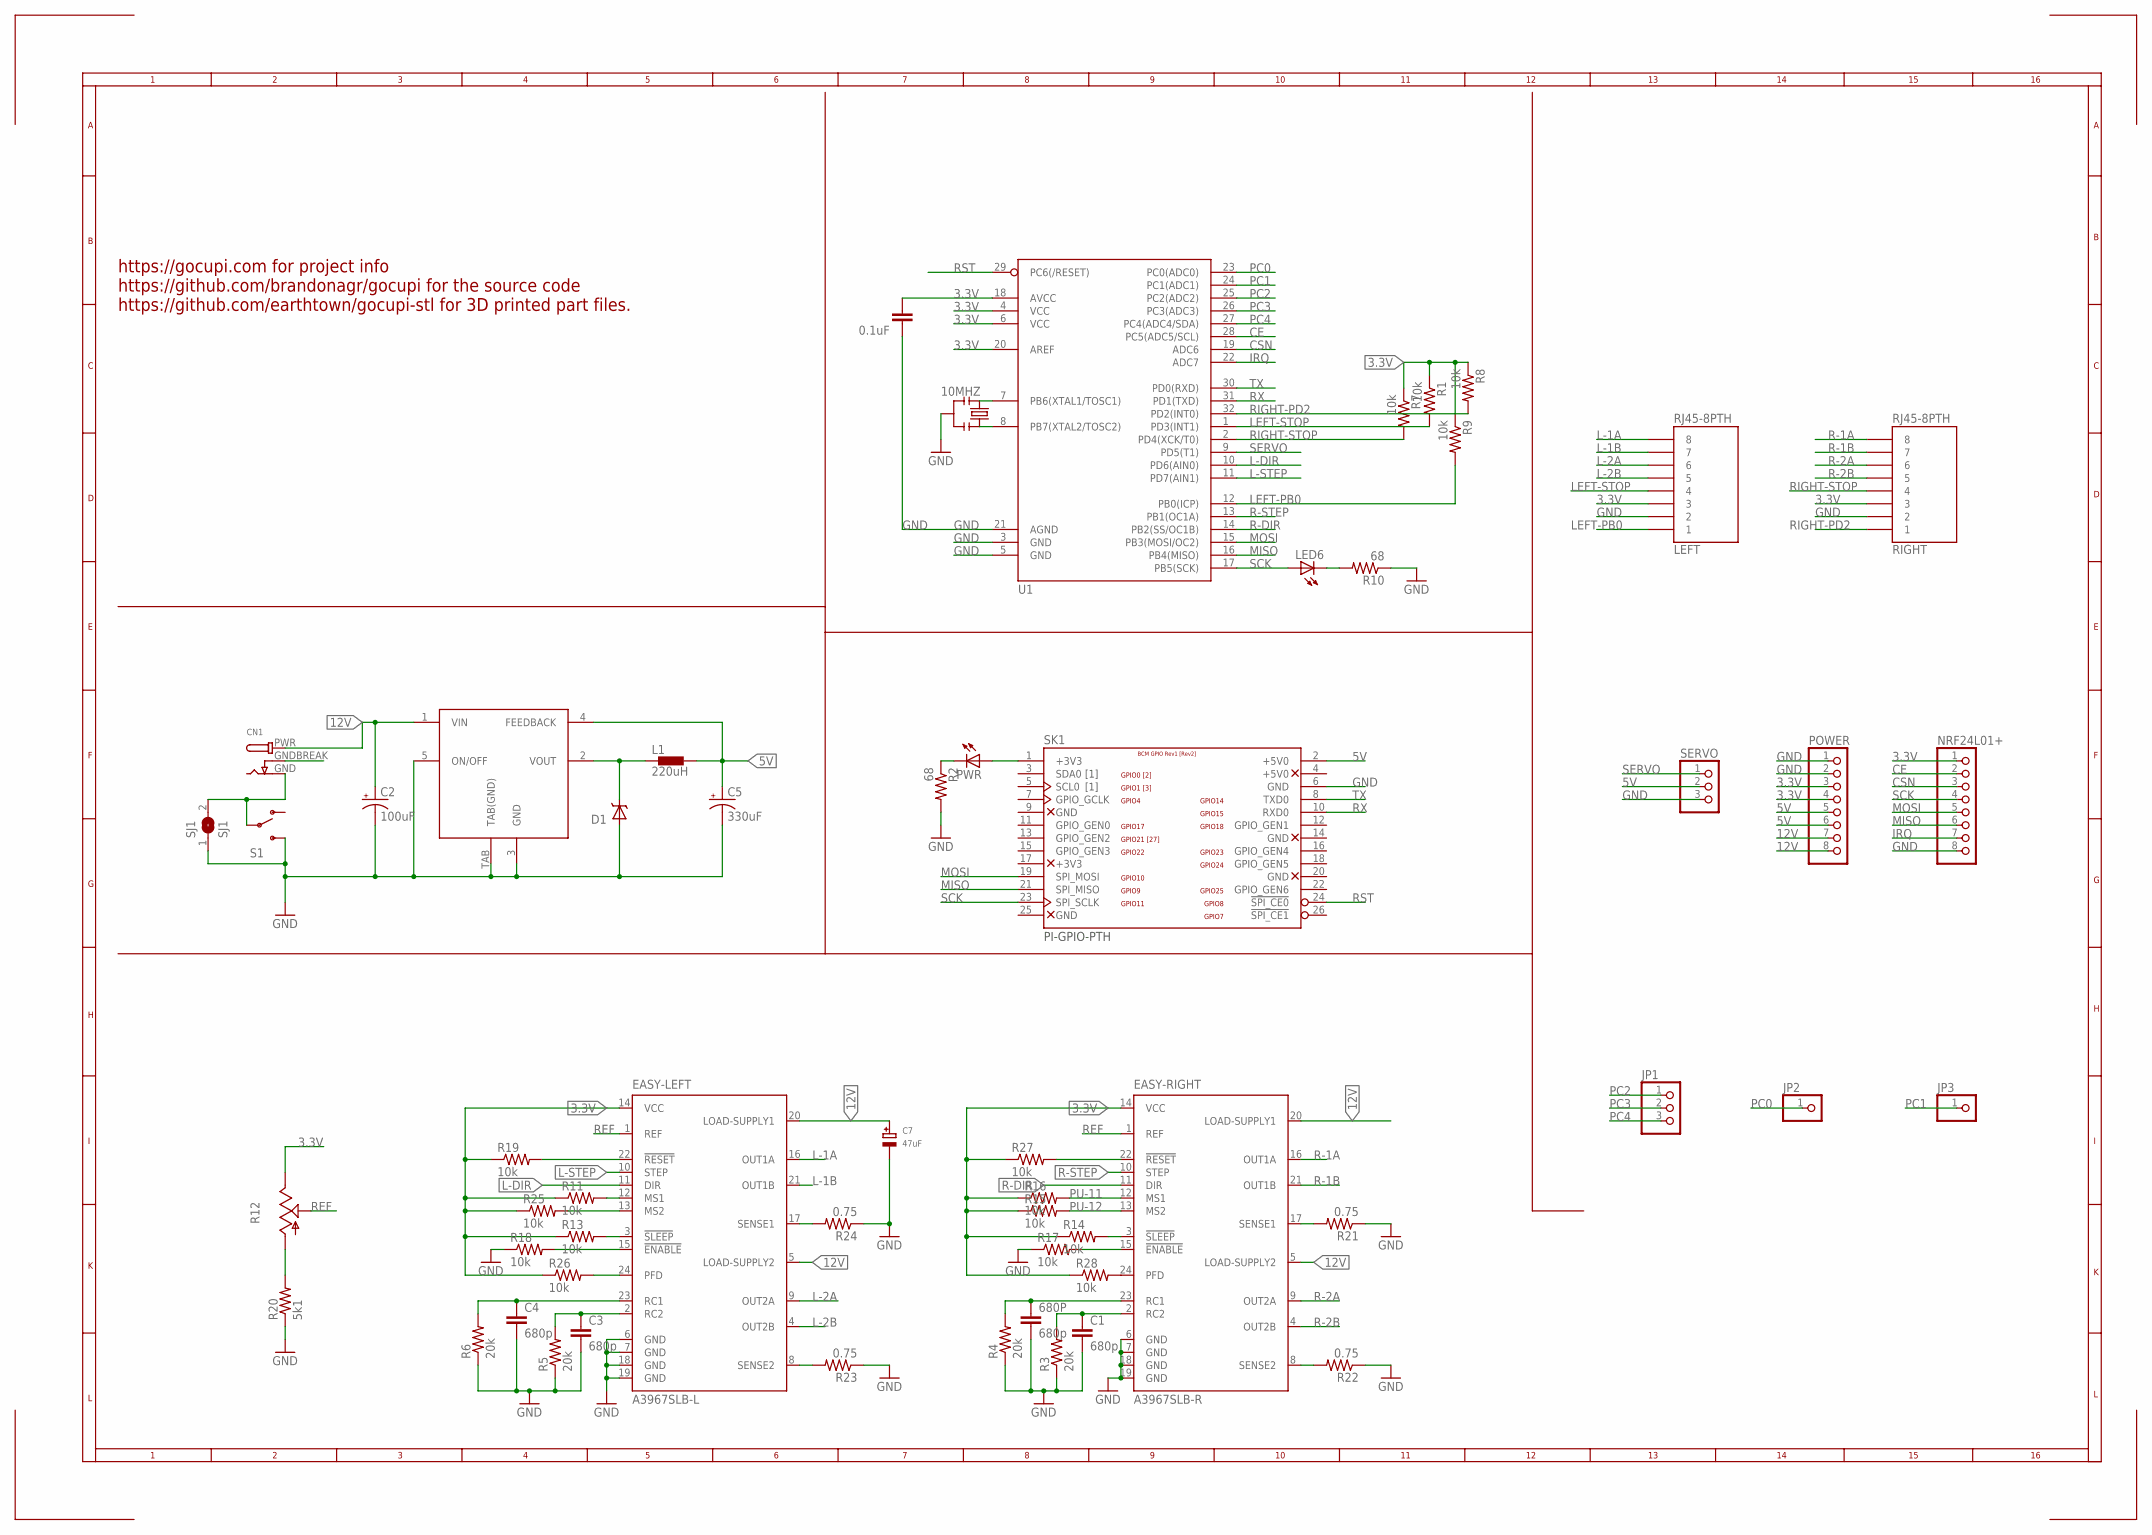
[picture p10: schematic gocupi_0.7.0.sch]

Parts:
10MHZ: RESONATORSMD; RESONATOR-SMD
680P: 680p; 0805
C1, C3, C4: 680p; 0805
C2: 100uF; PANASONIC_D
C5: 330uF; PANASONIC_F
C7: 47uF; PANASONIC_C
C8: 0.1uF; 0805
CN1: DCBARRELSMT_CORRECT; DCJACK_2MM_SMT
D1: 1N5819; SMA-DIODE
EASY-LEFT: A3967SLB-L; SO24W
EASY-RIGHT: A3967SLB-R; SO24W
JP1: PINHD-1X3CB; 1X03-CLEANBIG
JP2, JP3: PINHD-1X1CB; 1X01-CLEANBIG
L1: 220uH; SDR1305
LED6: LEDCHIPLED_1206; CHIPLED_1206
LEFT: RJ45-8PTH; RJ45-8
NRF24L01+: PINHD-1X8BIG; 1X08-BIG
POWER: PINHD-1X8CLEANBIG; 1X08-CLEANBIG
PWR: LEDCHIPLED_1206; CHIPLED_1206
R1, R7, R8, R9, R11, R13, R14, R15, R16, R17, R18, R19, R25, R26, R27, R28: 10k; 0805
R2, R10: 68; 0805
R3, R4, R5, R6: 20k; 0805
R12: TRIM_US-SM-42/43A; SM-42/43A
R20: 5k1; 0805
R21, R22, R23, R24: 0.75; 0805
RIGHT: RJ45-8PTH; RJ45-8
S1: SWITCH-SPST-SMD-A
SERVO: PINHD-1X3; 1X03
SJ1: SJ1; SJ
SK1: PI-GPIO-PTH; GPIO-CONNECTOR
U1: ATMEGA328_SMT; TQFP32-08
U$2: TL2575; TO263_5

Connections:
3.3V: C8.1, EASY-LEFT.14 (VCC), EASY-RIGHT.14 (VCC), LEFT.3, NRF24L01+.1, POWER.3, POWER.4, PWR.A, R1.1, R7.1, R8.1, R9.1, R11.1, R12.3 (E), R13.1, R14.1, R15.1, R16.1, R19.1, R25.1, R26.1, R27.1, R28.1, RIGHT.3, SK1.1 (+3V3), U1.4 (VCC), U1.6 (VCC), U1.18 (AVCC), U1.20 (AREF)
5V: C5.+, L1.P$2 (2), POWER.5, POWER.6, SERVO.2, SK1.2 (+5V0), U$2.4 (FEEDBACK)
12V: C2.+, C7.+, CN1.PWR, EASY-LEFT.5 (LOAD-SUPPLY2), EASY-LEFT.20 (LOAD-SUPPLY1), EASY-RIGHT.5 (LOAD-SUPPLY2), EASY-RIGHT.20 (LOAD-SUPPLY1), POWER.7, POWER.8, U$2.1 (VIN)
B-GND: CN1.GNDBREAK
CE: NRF24L01+.2, U1.28 (PC5(ADC5/SCL))
CSN: NRF24L01+.3, U1.19 (ADC6)
GND: 10MHZ.2, 680P.2, C1.2, C2.-, C3.2, C4.2, C5.-, C7.-, C8.2, D1.A, EASY-LEFT.6 (GND), EASY-LEFT.7 (GND), EASY-LEFT.18 (GND), EASY-LEFT.19 (GND), EASY-RIGHT.6 (GND), EASY-RIGHT.7 (GND), EASY-RIGHT.18 (GND), EASY-RIGHT.19 (GND), LEFT.2, NRF24L01+.8, POWER.1, POWER.2, R2.2, R3.1, R4.1, R5.1, R6.1, R10.1, R17.1, R18.1, R20.1, R21.1, R22.1, R23.1, R24.1, RIGHT.2, S1.3 (S), SERVO.3, SJ1.1, SK1.6 (GND), U1.3 (GND), U1.5 (GND), U1.21 (AGND), U$2.3 (GND), U$2.5 (ON/OFF), U$2.TAB (TAB(GND))
IRQ: NRF24L01+.7, U1.22 (ADC7)
L-1A: EASY-LEFT.16 (OUT1A), LEFT.8
L-1B: EASY-LEFT.21 (OUT1B), LEFT.7
L-2A: EASY-LEFT.9 (OUT2A), LEFT.6
L-2B: EASY-LEFT.4 (OUT2B), LEFT.5
L-DIR: EASY-LEFT.11 (DIR), U1.10 (PD6(AIN0))
L-STEP: EASY-LEFT.10 (STEP), U1.11 (PD7(AIN1))
LEFT-PB0: LEFT.1, R9.2, U1.12 (PB0(ICP))
LEFT-STOP: LEFT.4, R1.2, U1.1 (PD3(INT1))
MISO: NRF24L01+.6, SK1.21 (SPI_MISO), U1.16 (PB4(MISO))
MOSI: NRF24L01+.5, SK1.19 (SPI_MOSI), U1.15 (PB3(MOSI/OC2))
unnamed: D1.C, L1.P$1 (1), U$2.2 (VOUT)
unnamed: CN1.GND, S1.2, SJ1.2
unnamed: LED6.C, R10.2
unnamed: PWR.C, R2.1
unnamed: EASY-RIGHT.24 (PFD), R28.2
unnamed: EASY-LEFT.22 (!RESET), R19.2
unnamed: EASY-LEFT.12 (MS1), R11.2
unnamed: EASY-LEFT.24 (PFD), R26.2
unnamed: EASY-RIGHT.22 (!RESET), R27.2
unnamed: EASY-LEFT.13 (MS2), R25.2
unnamed: EASY-RIGHT.15 (!ENABLE), R17.2
unnamed: EASY-RIGHT.3 (!SLEEP), R14.2
unnamed: EASY-LEFT.3 (!SLEEP), R13.2
unnamed: R12.1 (A), R20.2
unnamed: EASY-LEFT.15 (!ENABLE), R18.2
unnamed: C4.1, EASY-LEFT.23 (RC1), R6.2
unnamed: C3.1, EASY-LEFT.2 (RC2), R5.2
unnamed: EASY-LEFT.17 (SENSE1), R24.2
unnamed: EASY-RIGHT.17 (SENSE1), R21.2
unnamed: EASY-LEFT.8 (SENSE2), R23.2
unnamed: 680P.1, EASY-RIGHT.23 (RC1), R4.2
unnamed: EASY-RIGHT.8 (SENSE2), R22.2
unnamed: C1.1, EASY-RIGHT.2 (RC2), R3.2
unnamed: 10MHZ.1, U1.7 (PB6(XTAL1/TOSC1))
unnamed: 10MHZ.3, U1.8 (PB7(XTAL2/TOSC2))
PC0: JP2.1, U1.23 (PC0(ADC0))
PC1: JP3.1, U1.24 (PC1(ADC1))
PC2: JP1.1, U1.25 (PC2(ADC2))
PC3: JP1.2, U1.26 (PC3(ADC3))
PC4: JP1.3, U1.27 (PC4(ADC4/SDA))
PU-11: EASY-RIGHT.12 (MS1), R16.2
PU-12: EASY-RIGHT.13 (MS2), R15.2
R-1A: EASY-RIGHT.16 (OUT1A), RIGHT.8
R-1B: EASY-RIGHT.21 (OUT1B), RIGHT.7
R-2A: EASY-RIGHT.9 (OUT2A), RIGHT.6
R-2B: EASY-RIGHT.4 (OUT2B), RIGHT.5
R-DIR: EASY-RIGHT.11 (DIR), U1.14 (PB2(SS/OC1B))
R-STEP: EASY-RIGHT.10 (STEP), U1.13 (PB1(OC1A))
REF: EASY-LEFT.1 (REF), EASY-RIGHT.1 (REF), R12.2 (S)
RIGHT-PD2: R8.2, RIGHT.1, U1.32 (PD2(INT0))
RIGHT-STOP: R7.2, RIGHT.4, U1.2 (PD4(XCK/T0))
RST: SK1.24 (!SPI_CE0), U1.29 (PC6(/RESET))
RX: SK1.10 (RXD0), U1.31 (PD1(TXD))
SCK: LED6.A, NRF24L01+.4, SK1.23 (SPI_SCLK), U1.17 (PB5(SCK))
SERVO: SERVO.1, U1.9 (PD5(T1))
TX: SK1.8 (TXD0), U1.30 (PD0(RXD))

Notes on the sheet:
https://gocupi.com for project info https://github.com/brandonagr/gocupi for the source code https://github.com/earthtown/gocupi-stl for 3D printed part files.

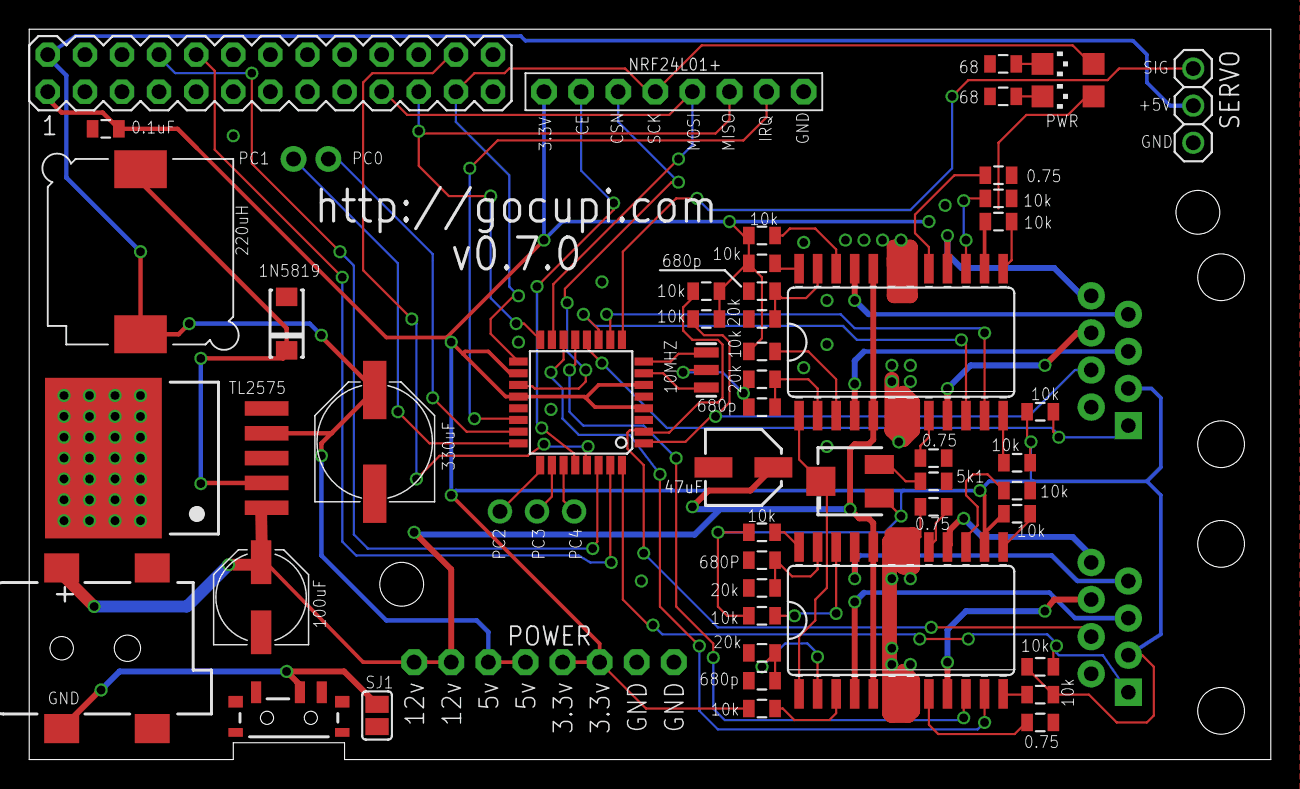
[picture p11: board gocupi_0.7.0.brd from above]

Board: 4 copper layers, 85.0 x 50.0 mm, 57 parts (0 on the bottom side), 63 nets.

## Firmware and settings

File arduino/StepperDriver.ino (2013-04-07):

/*
  Gocupi Arduino Code
  Reads movement commands over serial and controls two stepper motors 
*/

// comment out to disable PENUP support
#define ENABLE_PENUP

// Constants and global variables
// --------------------------------------
const int LED_PINS_COUNT = 4;
const int LED_PINS[LED_PINS_COUNT] = {
  2,3,4,8}; // the pins of all of the leds, first 3 are status lights, 5th is receive indicator
const int LEFT_STEP_PIN = 7;
const int LEFT_DIR_PIN = 6;
const int RIGHT_STEP_PIN = 9;
const int RIGHT_DIR_PIN = 10;

#ifdef ENABLE_PENUP
#include <Servo.h>
Servo penUpServo;
char penTransitionDirection; // -1, 0, 1
const int PENUP_SERVO_PIN = 5;
const long PENUP_TRANSITION_US = 524288; // time to go from pen up to down, or down to up
const int PENUP_TRANSITION_US_LOG = 19; // 2^19 = 524288
const long PENUP_COOLDOWN_US = 1250000;
const long PENUP_ANGLE = 40;
const long PENDOWN_ANGLE = 140;
#endif

const unsigned int TIME_SLICE_US = 2048; // number of microseconds per time step
const unsigned int TIME_SLICE_US_LOG = 11; // log base 2 of TIME_SLICE_US
const unsigned int POS_FACTOR = 32; // fixed point factor each position is multiplied by
const unsigned int POS_FACTOR_LOG = 5; // log base 2 of POS_FACTOR, used after multiplying two fixed point numbers together

const char RESET_COMMAND = 0x80; // -128, command to reset
const char PENUP_COMMAND = 0x81; // -127, command to lift pen
const char PENDOWN_COMMAND = 0x7F; // 127, command to lower pen

const unsigned int MOVE_DATA_CAPACITY = 1024;
char moveData[MOVE_DATA_CAPACITY]; // buffer of move data, circular buffer
unsigned int moveDataStart = 0; // where data is currently being read from
unsigned int moveDataLength = 0; // the number of items in the moveDataBuffer
unsigned int moveDataRequestPending = 0; // number of bytes requested

char leftDelta, rightDelta; // delta in the current slice
long leftStartPos, rightStartPos; // start position for this slice
long leftCurPos, rightCurPos; // current position of the spools

unsigned long curTime; // current time in microseconds
unsigned long sliceStartTime; // start of current slice in microseconds


// setup
// --------------------------------------
void setup() {
  Serial.begin(57600);
  Serial.setTimeout(0);

  // setup pins
  for(int ledIndex = 0; ledIndex < LED_PINS_COUNT; ledIndex++) {
    pinMode(LED_PINS[ledIndex], OUTPUT);
    digitalWrite(LED_PINS[ledIndex], HIGH);
  }	
  pinMode(LEFT_STEP_PIN, OUTPUT);
  pinMode(LEFT_DIR_PIN, OUTPUT);
  pinMode(RIGHT_STEP_PIN, OUTPUT);
  pinMode(RIGHT_DIR_PIN, OUTPUT);	

#ifdef ENABLE_PENUP
  penUpServo.attach(PENUP_SERVO_PIN);
  penUpServo.write(PENUP_ANGLE);
  delay(1000);
  penUpServo.write(PENDOWN_ANGLE);
  delay(1000);
  penUpServo.write(PENUP_ANGLE);
#endif  

  ResetMovementVariables();

  delay(500);
  UpdateReceiveLed(false);
  UpdateStatusLeds(0);
}

// Reset all movement variables
// --------------------------------------
void ResetMovementVariables()
{
  leftDelta = rightDelta = leftStartPos = rightStartPos = leftCurPos = rightCurPos = 0;
  sliceStartTime = curTime;

#ifdef ENABLE_PENUP
  penTransitionDirection = 0;
  penUpServo.write(PENUP_ANGLE);
#endif  
}

// Main execution loop
// --------------------------------------
void loop() {
  curTime = micros();
  if (curTime < sliceStartTime) { // protect against 70 minute overflow
    sliceStartTime = 0;
  }

  long curSliceTime = curTime - sliceStartTime;

#ifdef ENABLE_PENUP
  if (penTransitionDirection) {
    UpdatePenTransition(curSliceTime);
    if (!penTransitionDirection) {
      sliceStartTime = curTime;
    }
  } else {	
#endif
    // move to next slice if necessary
    while(curSliceTime > TIME_SLICE_US) {
      SetSliceVariables();
      curSliceTime -= TIME_SLICE_US;
      sliceStartTime += TIME_SLICE_US;

#ifdef ENABLE_PENUP	
      if (penTransitionDirection) {
        sliceStartTime = curTime;
        return;
      }
#endif      
    }
	
    UpdateStepperPins(curSliceTime);
#ifdef ENABLE_PENUP    
  }
#endif  

  ReadSerialMoveData();
  RequestMoreSerialMoveData();
}

// Update stepper pins
// --------------------------------------
void UpdateStepperPins(long curSliceTime) {
  long leftTarget = ((long(leftDelta) * curSliceTime) >> TIME_SLICE_US_LOG) + leftStartPos;
  long rightTarget = ((long(rightDelta) * curSliceTime) >> TIME_SLICE_US_LOG) + rightStartPos;

  int leftSteps = (leftTarget - leftCurPos) >> POS_FACTOR_LOG;
  int rightSteps = (rightTarget - rightCurPos) >> POS_FACTOR_LOG;

  boolean leftPositiveDir = true;
  if (leftSteps < 0) {
    leftPositiveDir = false;
    leftSteps = -leftSteps;
  }
  boolean rightPositiveDir = true;
  if (rightSteps < 0) {
    rightPositiveDir = false;
    rightSteps = -rightSteps;
  }

  do {
    if (leftSteps) {
      Step(LEFT_STEP_PIN, LEFT_DIR_PIN, leftPositiveDir);
      if (leftPositiveDir) {
        leftCurPos += POS_FACTOR;
      } else {
        leftCurPos -= POS_FACTOR;
      }
      leftSteps--;
      
      UpdateStatusLeds(leftCurPos >> 13);
    }

    if (rightSteps) {
      Step(RIGHT_STEP_PIN, RIGHT_DIR_PIN, rightPositiveDir);
      if (rightPositiveDir) {
        rightCurPos += POS_FACTOR;
      } else {
        rightCurPos -= POS_FACTOR;
      }
      rightSteps--;
    }

    if (leftSteps || rightSteps) {
      delayMicroseconds(50); // delay a small amount of time before refiring the steps to smooth things out
    } else {
      break;
    }
  } while(true);
}

// Update pen position
// --------------------------------------
#ifdef ENABLE_PENUP
void UpdatePenTransition(long curSliceTime) {
	
  //int targetAngle = ((float)(PENDOWN_ANGLE - PENUP_ANGLE) * ((float)curSliceTime / (float)PENUP_TRANSITION_US)) + PENUP_ANGLE;
  //if (targetAngle > PENDOWN_ANGLE) {
    //targetAngle = PENDOWN_ANGLE;
    
    if (curSliceTime > PENUP_COOLDOWN_US) {
      penTransitionDirection = 0; // are done moving the pen servo
    }
  //}

  if (penTransitionDirection == 1) {
	//targetAngle = 180 - targetAngle;
    penUpServo.write(PENUP_ANGLE);
  } else if (penTransitionDirection == -1) {
    penUpServo.write(PENDOWN_ANGLE);
  }

  //penUpServo.write(targetAngle);
}
#endif

// Update status leds
// --------------------------------------
void UpdateStatusLeds(int value) {
  // output the time to the leds in binary
  digitalWrite(LED_PINS[0], value & 0x1);
  digitalWrite(LED_PINS[1], value & 0x2);
  digitalWrite(LED_PINS[2], value & 0x4);
}

// Update receive leds
// --------------------------------------
void UpdateReceiveLed(boolean value) {
  digitalWrite(LED_PINS[3], value);
}

// Step
// --------------------------------------
void Step(int stepPin, int dirPin, boolean dir) {
  digitalWrite(dirPin, dir);

  digitalWrite(stepPin, LOW);
  digitalWrite(stepPin, HIGH);
}

// Set all variables based on the data currently in the buffer
// --------------------------------------
void SetSliceVariables() {
  // set slice start pos to previous slice start plus previous delta
  leftStartPos = leftStartPos + long(leftDelta);
  rightStartPos = rightStartPos + long(rightDelta);

  if (moveDataLength < 2) {
    leftDelta = rightDelta = 0;
  } else {
    leftDelta = MoveDataGet();
    rightDelta = MoveDataGet();
    
#ifdef ENABLE_PENUP	
    if (leftDelta == PENUP_COMMAND) {
      leftDelta = rightDelta = 0;
      penTransitionDirection = 1;
    } else if (leftDelta == PENDOWN_COMMAND) {
      leftDelta = rightDelta = 0;
      penTransitionDirection = -1;
    }
#else
    if (leftDelta == PENUP_COMMAND || leftDelta == PENDOWN_COMMAND) {
       leftDelta = rightDelta = 0;
    }
#endif    
  }
}                                                                                                                                                                                                                                                                                                                                                                                                                                                                                                                                                                                                                                                                                                                                                                                                                                                                                                                                                                                                                                                                                                                                                                                                                                                                                                                                                                                                                                                                                                                                                                                                                                                                                                                                                                                                                                                                                                                                                                                                                                                    

// Stop everything and blink the status led value times
// --------------------------------------
void Blink(char value) {
 int counts = value;
  if (counts<0) counts=-counts;

  UpdateReceiveLed(false);
  for(int i=0;i<counts;i++) {
   delay(1000);
   UpdateReceiveLed(true);
   delay(1000);
   UpdateReceiveLed(false);
    
  }
  delay(100000);
}

// Read serial data if its available
// --------------------------------------
void ReadSerialMoveData() {     

  if(Serial.available()) {
    char value = Serial.read();
    
    // Check if this value is the sentinel reset value
    if (value == RESET_COMMAND) {
      ResetMovementVariables();
      moveDataRequestPending = 0;
      moveDataLength = 0;
      UpdateReceiveLed(false);
      return;
    }

    MoveDataPut(value);
    moveDataRequestPending--;

    if (!moveDataRequestPending) {
      UpdateReceiveLed(false);
    }
  }
}

// Put a value onto the end of the move data buffer
// --------------------------------------
void MoveDataPut(char value) {
  int writePosition = moveDataStart + moveDataLength;
  if (writePosition >= MOVE_DATA_CAPACITY) {
    writePosition = writePosition - MOVE_DATA_CAPACITY;
  }

  moveData[writePosition] = value;

  if (moveDataLength == MOVE_DATA_CAPACITY) { // full, overwrite existing data
    moveDataStart++;
    if (moveDataStart == MOVE_DATA_CAPACITY) {
      moveDataStart = 0;
    }
  } 
  else {
    moveDataLength++;
  }
}

// Return a piece of data sitting in the moveData buffer, removing it from the buffer
// --------------------------------------
char MoveDataGet() {
  if (moveDataLength == 0) {
    return 0;
  }

  char result = moveData[moveDataStart];
  moveDataStart++;
  if (moveDataStart == MOVE_DATA_CAPACITY) {
    moveDataStart = 0;
  }
  moveDataLength--;

  return result;
}

// Return the amount of data sitting in the moveData buffer
// --------------------------------------
void RequestMoreSerialMoveData() {
  if (moveDataRequestPending > 0 || MOVE_DATA_CAPACITY - moveDataLength < 128)
    return;

  // request 128 bytes of data
  Serial.write(128);
  moveDataRequestPending = 128;
  UpdateReceiveLed(true);
}

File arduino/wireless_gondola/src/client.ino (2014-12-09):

/**
Test out using NRF2401L+ for wireless communication
**/

#include <SPI.h>
#include <nRF24L01.h>
#include <RF24.h>
#include <RF24_config.h>
#include <Servo.h>

Servo penUpServo;
const int PENUP_SERVO_PIN = 9;
// this is SPI SCK pin, so cant use it as status led
const int STATUS_LED_PIN = 8;

const int CE_PIN = A5;
const int CSN_PIN = A6;

RF24 radio(CE_PIN, CSN_PIN);

byte readDataFromMirf = 0;
long blinkDelayMillis = 250;
bool currentLedStatus = false;
unsigned long previousTime = 0;

void setup(){
  
//  Serial.begin(57600);
//  Serial.println("Setup");
  
  // setup servo
  penUpServo.attach(PENUP_SERVO_PIN);
  pinMode(STATUS_LED_PIN, OUTPUT);
  digitalWrite(STATUS_LED_PIN, 0);
  delay(1000);
  digitalWrite(STATUS_LED_PIN, 1);
  delay(1000);
  digitalWrite(STATUS_LED_PIN, 0);
  delay(1000);

  radio.begin();
  radio.setRetries(15, 15); // 2*250=500us between tries, 5 tries
  radio.setPayloadSize(4);
  radio.openReadingPipe(1, 0xF0F0F0F0E1LL);
  radio.openWritingPipe(0xF0F0F0F0D2LL);
  radio.startListening();
  
//  Serial.println("Setup done");
}

void loop(){
  // update status led
  // when sketch first start led blinks rapidly, until after it receives at least one byte over
  unsigned long curTime = millis();
  blinkDelayMillis -= (curTime - previousTime);
  if (blinkDelayMillis < 0) {
    currentLedStatus = !currentLedStatus;
    digitalWrite(STATUS_LED_PIN, currentLedStatus);
    
    if (currentLedStatus) {
      blinkDelayMillis = 250;
    } else {
      blinkDelayMillis = 750;
    }
/*
    if (readDataFromMirf) {
      if (currentLedStatus) {
// += would be more accurate, but want to prevent propogation of potential errors like time overflow
        blinkDelayMillis = 500;
      } else {
        blinkDelayMillis = 2000;
      }
    } else {
      blinkDelayMillis = 1000;
    }
*/
  }
  previousTime = curTime;

  radio.startListening();
  delay(100);

  long receiveData;
  if (radio.available()) {
    
//    while(radio.read(&receiveData, sizeof(long))) {
    radio.read(&receiveData, sizeof(long));
    
//      Serial.print("Got data: ");
//      Serial.println(receiveData);

      if (receiveData) {
//        penUpServo.write(150);

        currentLedStatus = !currentLedStatus;
        digitalWrite(STATUS_LED_PIN, currentLedStatus);
        blinkDelayMillis = 1000;
      } else {
//        penUpServo.write(0);

        currentLedStatus = !currentLedStatus;
        digitalWrite(STATUS_LED_PIN, currentLedStatus);
        blinkDelayMillis = 2000;
      }
//  }
  }
}

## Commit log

2012-09-12 Communication with servos over I2C working, next need to create library
2012-10-20 Add arduino code, Modify to use 2ms slices and reduce number of printlns in driver
2012-10-21 Change WriteStepsToSerial to assume a data request has already been made, so that it can start communication without having to reset the arduino every time
2012-10-22 Add PrintUsage for unexpected command
2012-10-29 Got interpolation approach working, switched to 1/8 microsteps instead of 1/4, makes movement smoother and torque seems fine
2012-10-30 Fix typo in deceleration only formula, add gopher and raspberry svg files
2012-10-30 Add sentinel serial value so that steppers can start moving without having to manually push resest button on arduino each time
2012-10-31 Working test file for using /dev/input/event to track mouse
2012-10-31 Fix sentinel auto restarting arduino, an extra 254 value seems to be written to the serial port when it is opened, so changed the arduino code to compare all bytes to sentinel, not just the first byt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
    [StepperDriver.ino]
2012-10-31 Improve mouse to handle button clicks to exit
2012-11-01 Rewrite mouse support to skip the pipeline approach and just write directly to the serial port, make mouse object just expose get current position
2012-11-02 Improve mouse tracking, will always be a 1 second lag due to the buffer in the arduino
2012-11-05 Flip spool directions to accomodate the new spool towards wall motor mounts
2012-11-07 Use cosAngle^3 to determine exit speed in order to reduce size of discontinuities in graph of velocity
2012-11-15 Add cad drawings used for guide, motor mounts, bearing holder
    [guide.dwg, motor mount.dwg, small bearing holder.dwg]
2013-03-06 Add const to stepperdriver sketch
2013-04-06 Add simple svg path support, add currently passing svg_tests
2013-04-07 Untested arduino support for servo pen up
2013-04-07 Test compiling does not auto save in the arduino ide...
2013-04-07 Fix arduino code to work with test servo
    [StepperDriver.ino]
2013-04-07 Fix penup arduino code by not doing the slow transition for now
    [StepperDriver.ino]
2013-04-08 Fix svg rendering to not incorrectly move y axis
2013-08-28 Fix basic timeline calculation, need to return actual time instead of just percentage of current segment
2013-11-22 Revert "Fix basic timeline calculation, need to return actual time instead of just percentage of current segment"
    This reverts commit 93cd8d4ccf01ef028c4e7a649882699cfd6024f6.
2014-04-24 Add bash script that can be used to initialize a new arduino instead of having to use the arduino ide to do it
2014-06-23 Implement setup command that makes it possible to specify motor distance and left/right distance from command line, auto copy default gocupi_config.xml to working directory if it doesn't already exist
2014-06-23 Fix not handling switch/case correctly for fallthrough case, same cases should be on same line seperated by comma
2014-07-06 gocupi main board files (Eagle and PDF)
    [gocupi_0.7.0.brd, gocupi_0.7.0.sch]
2014-07-17 Using a relative import path seems to break the ability to do go get, the absolute path works when running 'go build' from gocupi directory when you have your gopath set, it produces the gocupi.exe i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
2014-07-21 Begin testing using nrf24l01 for wireless gondola
2014-08-14 No progress on getting wireless nrf24l01+ working w/ gondola board
2014-08-14 Turns out SPI wasn't freezing, its just that the nrf board is always returning data available, even with no server running
2014-08-18 Update gocupi.go
    putting the project in Camelcase forces the sources to be Twice in the Src folder,
    making changes impossible to track... :)
2014-08-19 Gcode Makelangelo Compatible
    Now Gcode has support for MAkelangelo Gcode Generator (Using stock Pen Settings UP = 50), need still to find a way to make it all Gcode compatible
    Gcode has up en down support for using the pretty filters in makelangelo (Spiral for example)
    https://github.com/MarginallyClever/Makelangelo
    (i can give result output of it
2014-12-02 DrawingSurfaceMaxX calculation Fix #12
    Since the origin is the idler pulley and not the DrawingSurfaceMinX, should only subtract MinX once to get MaxX instead of subtracting twice, which gets the width of drawing area but not current MaxX according to coordinate system.
2016-09-12 Added hardware version 1.1
    [gocupi_0.7.0.brd, gocupi_0.7.0.sch, gocupi_v1.1.brd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]

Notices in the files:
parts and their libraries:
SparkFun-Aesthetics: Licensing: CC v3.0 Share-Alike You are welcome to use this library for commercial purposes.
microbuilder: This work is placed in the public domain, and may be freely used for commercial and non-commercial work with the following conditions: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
